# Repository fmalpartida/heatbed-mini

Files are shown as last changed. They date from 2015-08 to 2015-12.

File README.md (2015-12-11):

# heatbed-mini
Mini heatbed for small footprint 3D printers. This bed has been designed for the lewihe play but can be retrofitted to other small 
printers with a print area of 100x100 mm.

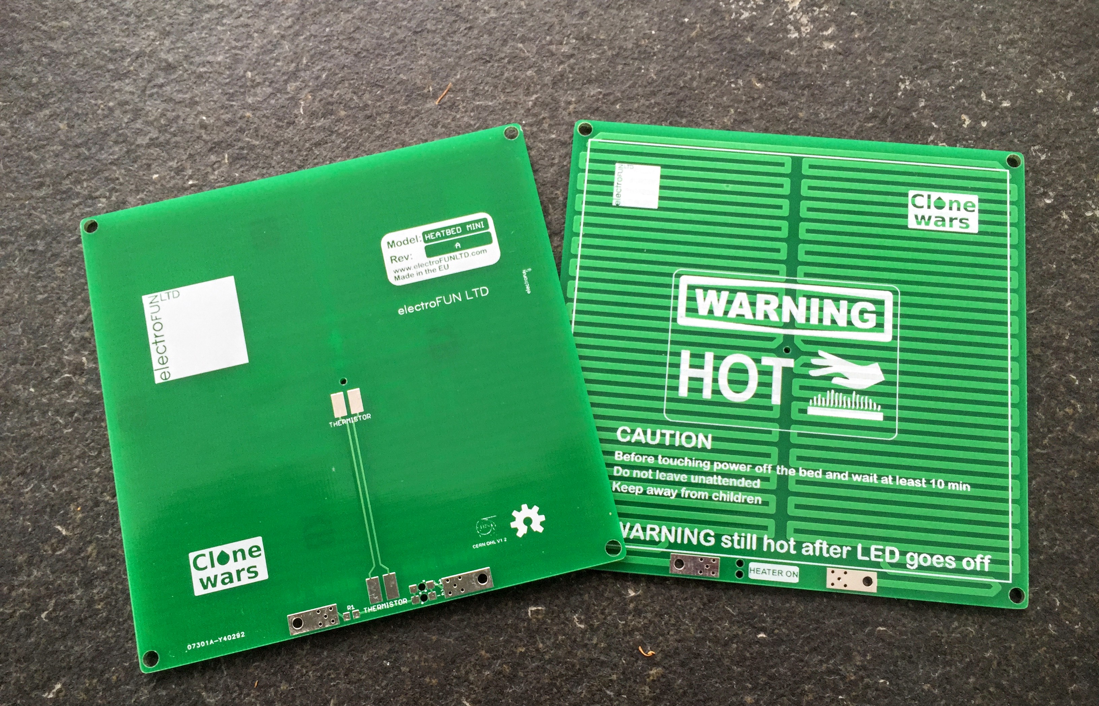
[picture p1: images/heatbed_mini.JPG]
PCB image


## Specifications

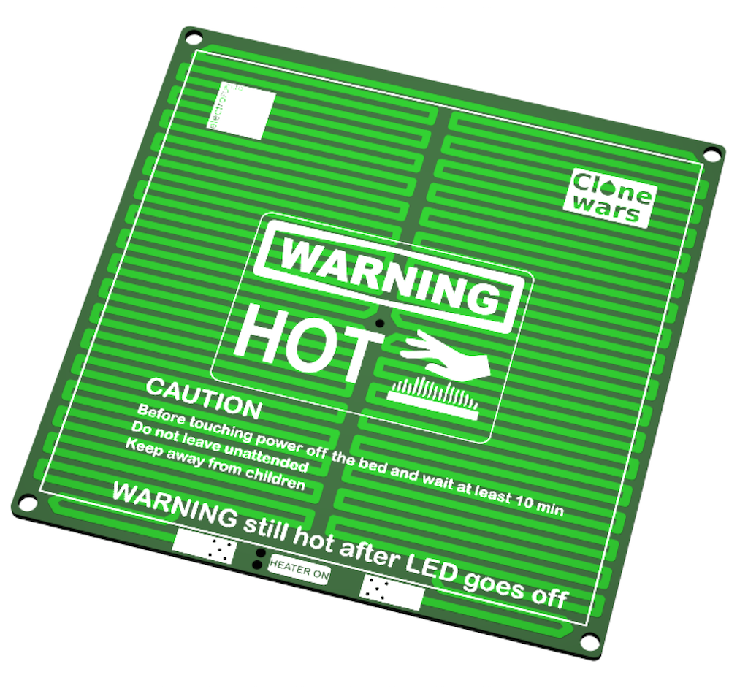
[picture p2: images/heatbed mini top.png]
3D PCB view


+ **Size:** 100x100 mm
+ **Rated voltage:** 12V
+ **Maximum operational temperature:** 150ºC
+ **Power dissipation:**
   + **Rev B:** 69W aprox: 12V @25ºC, 50W aprox: 12V @110ºC 
+ **Resistance:**
   + **Rev B**: 2.1 Ohms aprox, 2.8 Ohms aprox @110ºC
 
Do not exceed rated parameters.

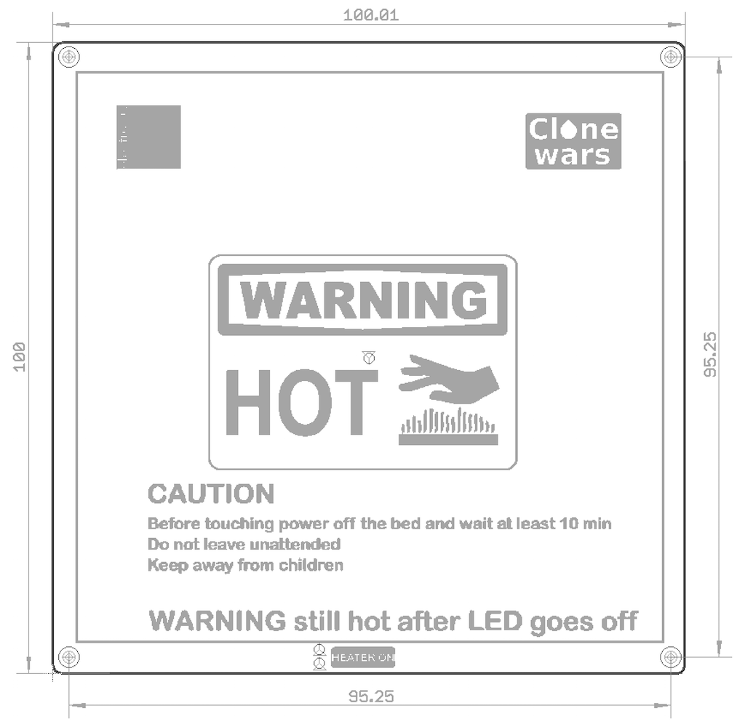
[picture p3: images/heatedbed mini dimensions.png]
PCB dimensions


## Images

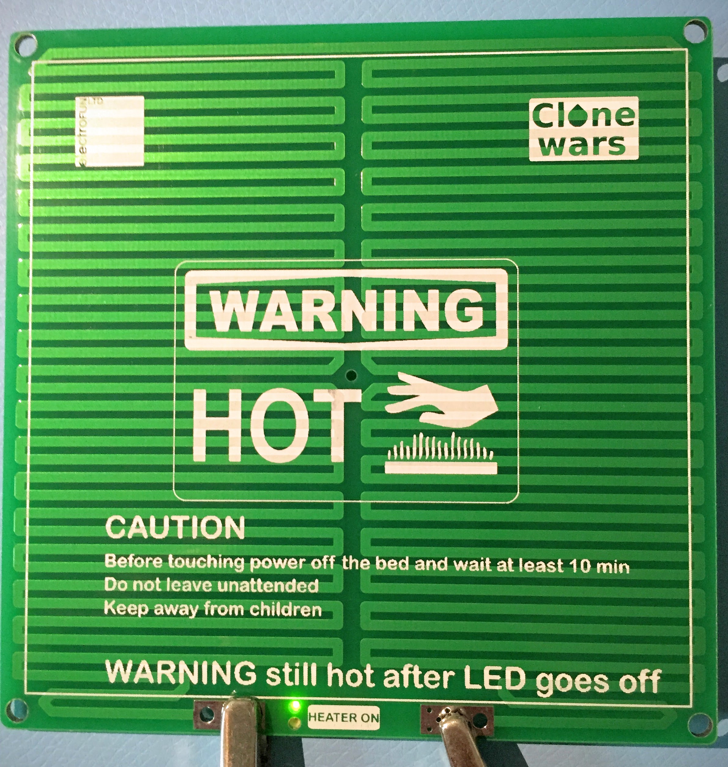
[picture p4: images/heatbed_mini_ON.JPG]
Activated


## License
Released under CERN Open Hardware License v1.2
http://www.ohwr.org/attachments/2388/cern_ohl_v_1_2.txt

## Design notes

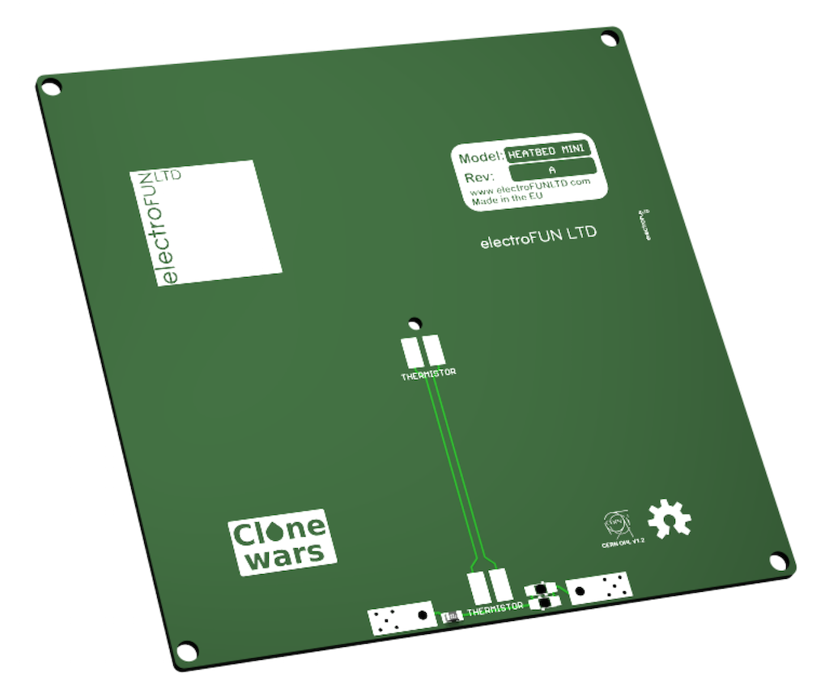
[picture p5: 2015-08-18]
images/heatbed mini bottom.png

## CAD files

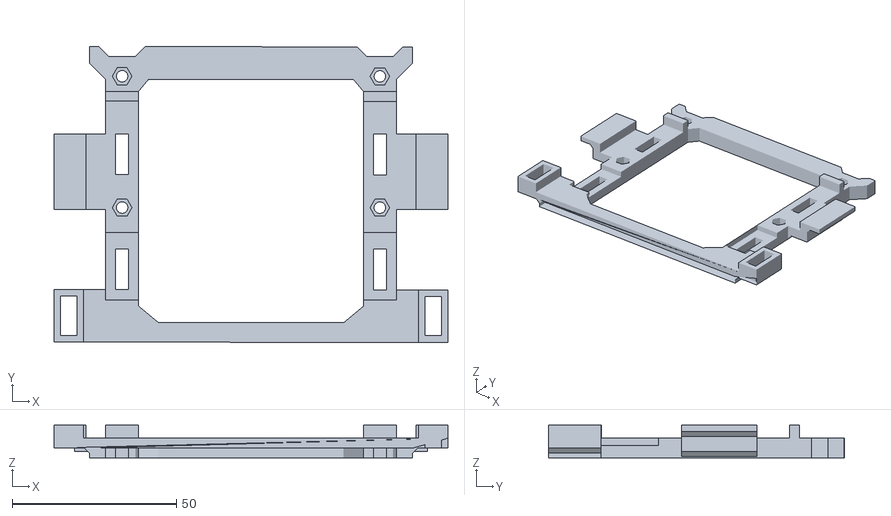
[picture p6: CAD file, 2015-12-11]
3D files/Soporte Base de impresión imanes lewihe Play.stl
120.0 x 90.0 x 10.0

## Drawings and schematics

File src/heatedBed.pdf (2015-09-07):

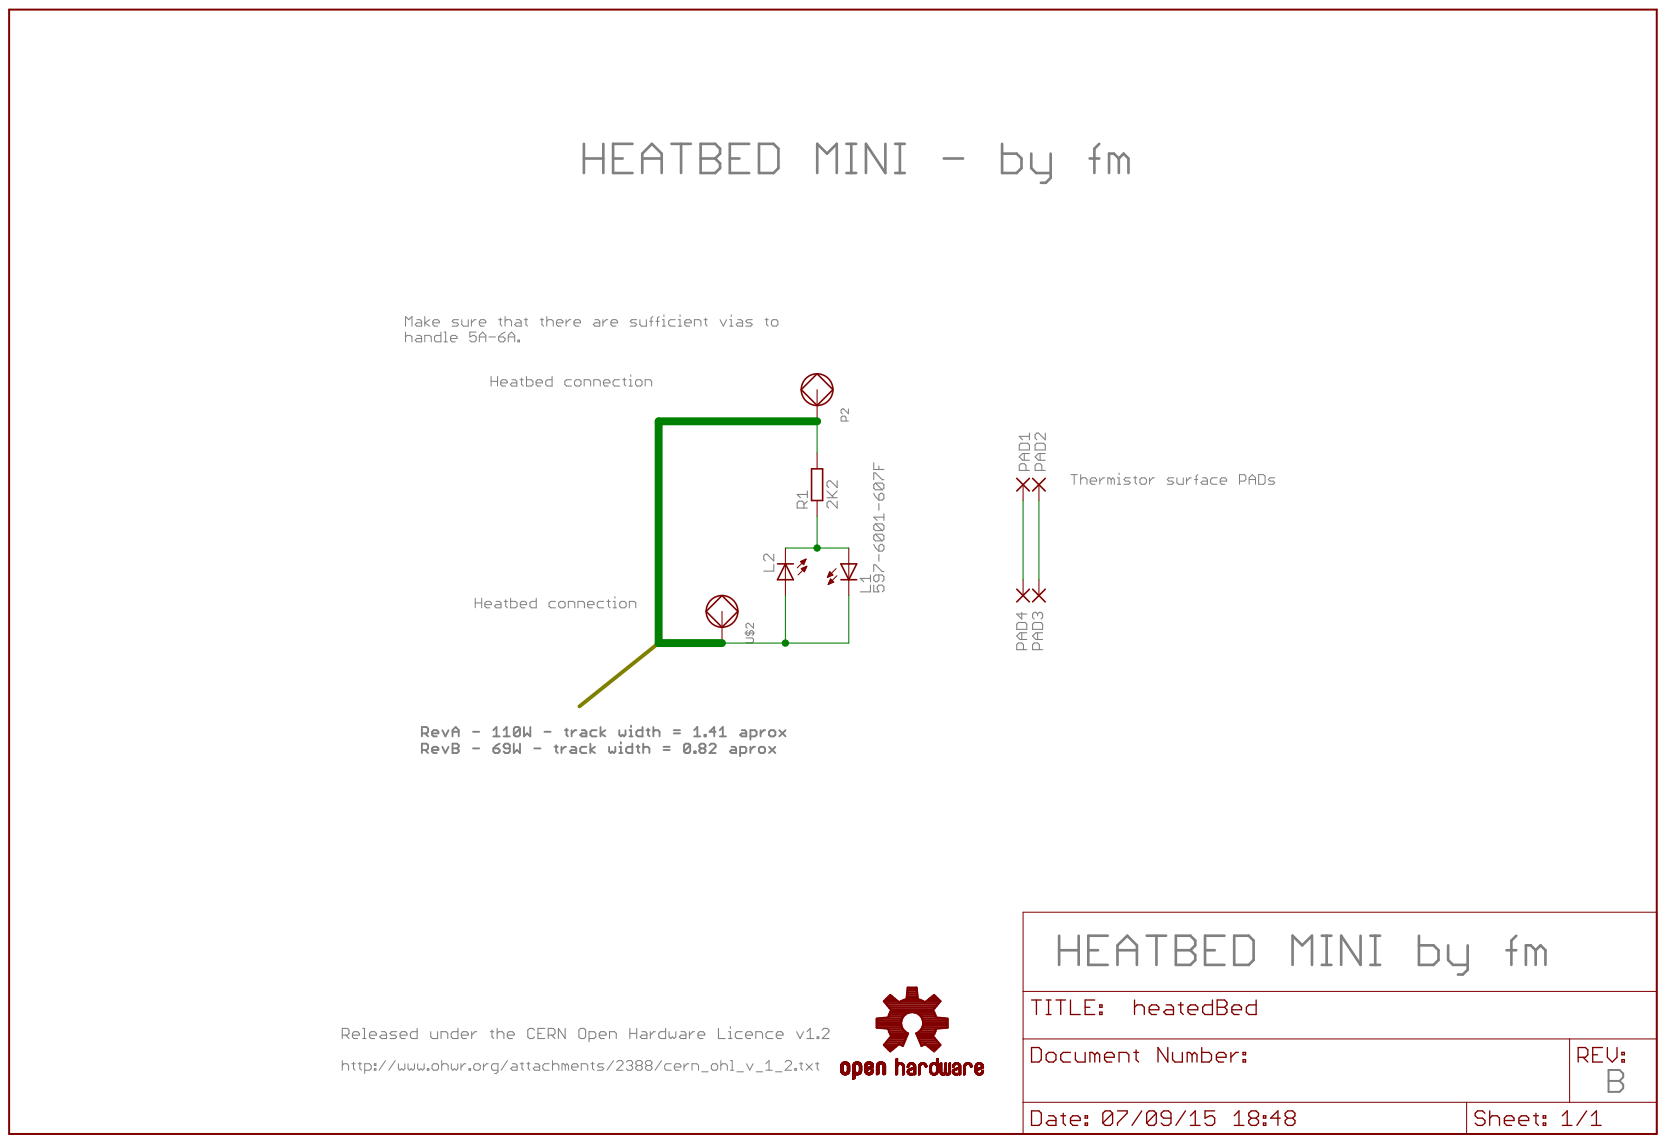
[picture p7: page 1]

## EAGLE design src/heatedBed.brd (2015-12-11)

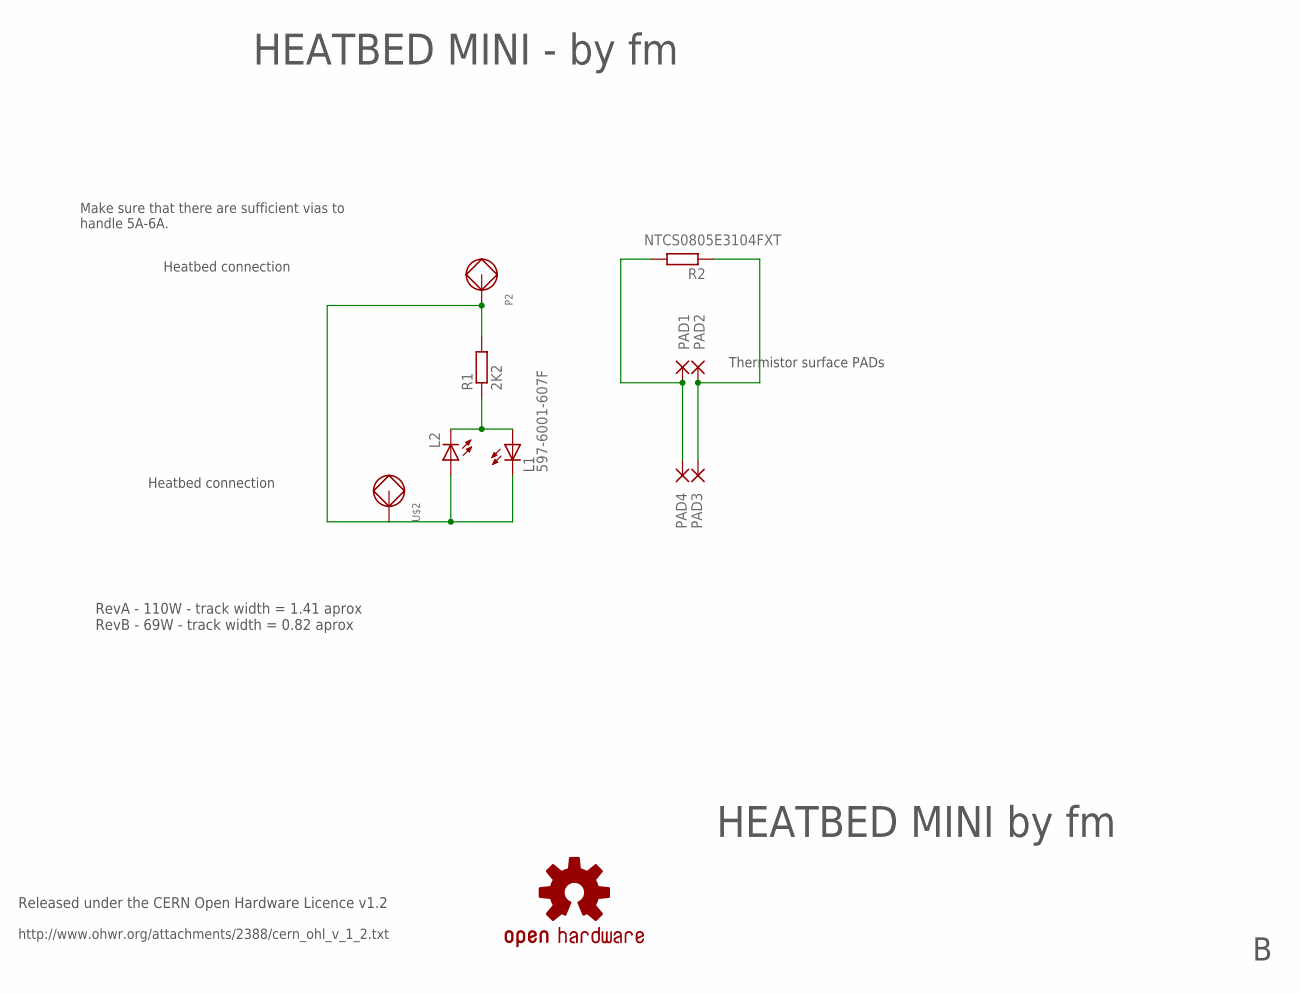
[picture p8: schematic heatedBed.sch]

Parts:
L1: 597-6001-607F; CHIPLED_1206_REVERSE
L2: LEDCHIPLED_1206_REV; CHIPLED_1206_REVERSE
P2: LONG_PAD
PAD1, PAD2, PAD3, PAD4: SMD5; SMD2,54-5,08
R1: 2K2; R0805
R2: NTCS0805E3104FXT; R0805
U$2: LONG_PAD
U$5: SPARKFUN_OSHW-LOGOL; SPARKFUN_OSHW-LOGO-L

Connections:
unnamed: PAD1.1, PAD4.1, R2.2
unnamed: L1.A, L2.C, R1.1
unnamed: PAD2.1, PAD3.1, R2.1
P1: L1.C, L2.A, P2.P$1, P2.P$2, P2.P$3, R1.2, U$2.P$1, U$2.P$2, U$2.P$3

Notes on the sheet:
Released under the CERN Open Hardware Licence v1.2
HEATBED MINI by fm
Heatbed connection
Make sure that there are sufficient vias to handle 5A-6A.
Thermistor surface PADs
http://www.ohwr.org/attachments/2388/cern_ohl_v_1_2.txt
HEATBED MINI - by fm
RevA - 110W - track width = 1.41 aprox RevB - 69W - track width = 0.82 aprox

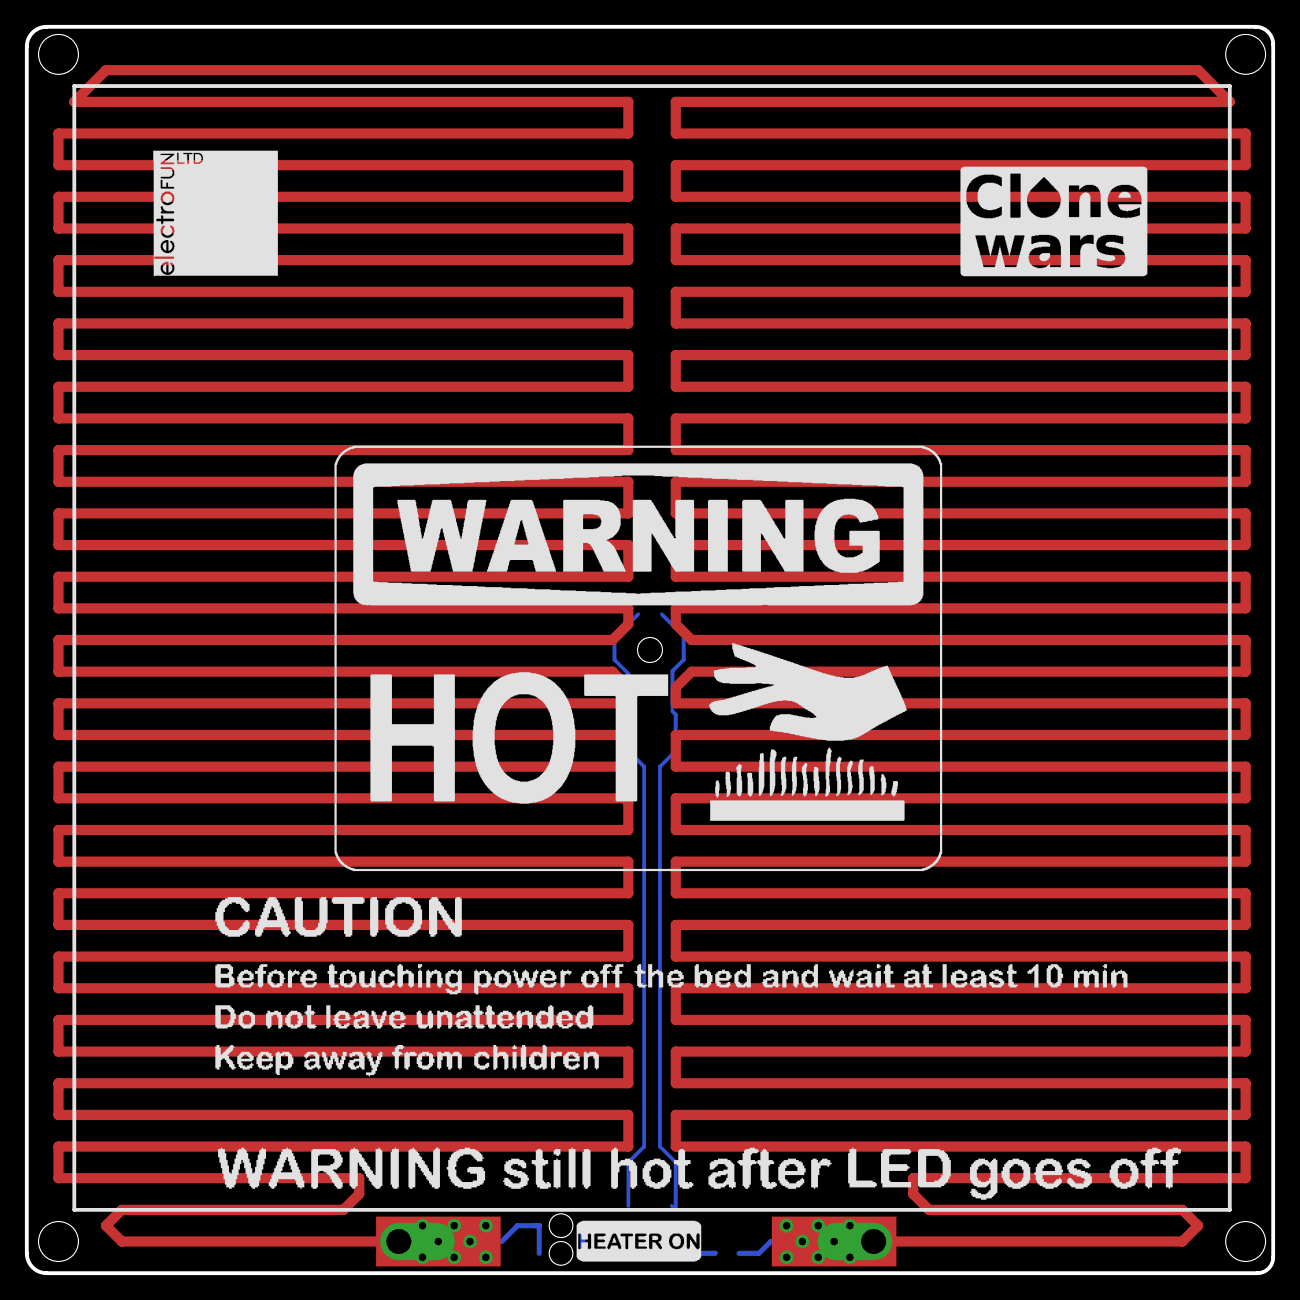
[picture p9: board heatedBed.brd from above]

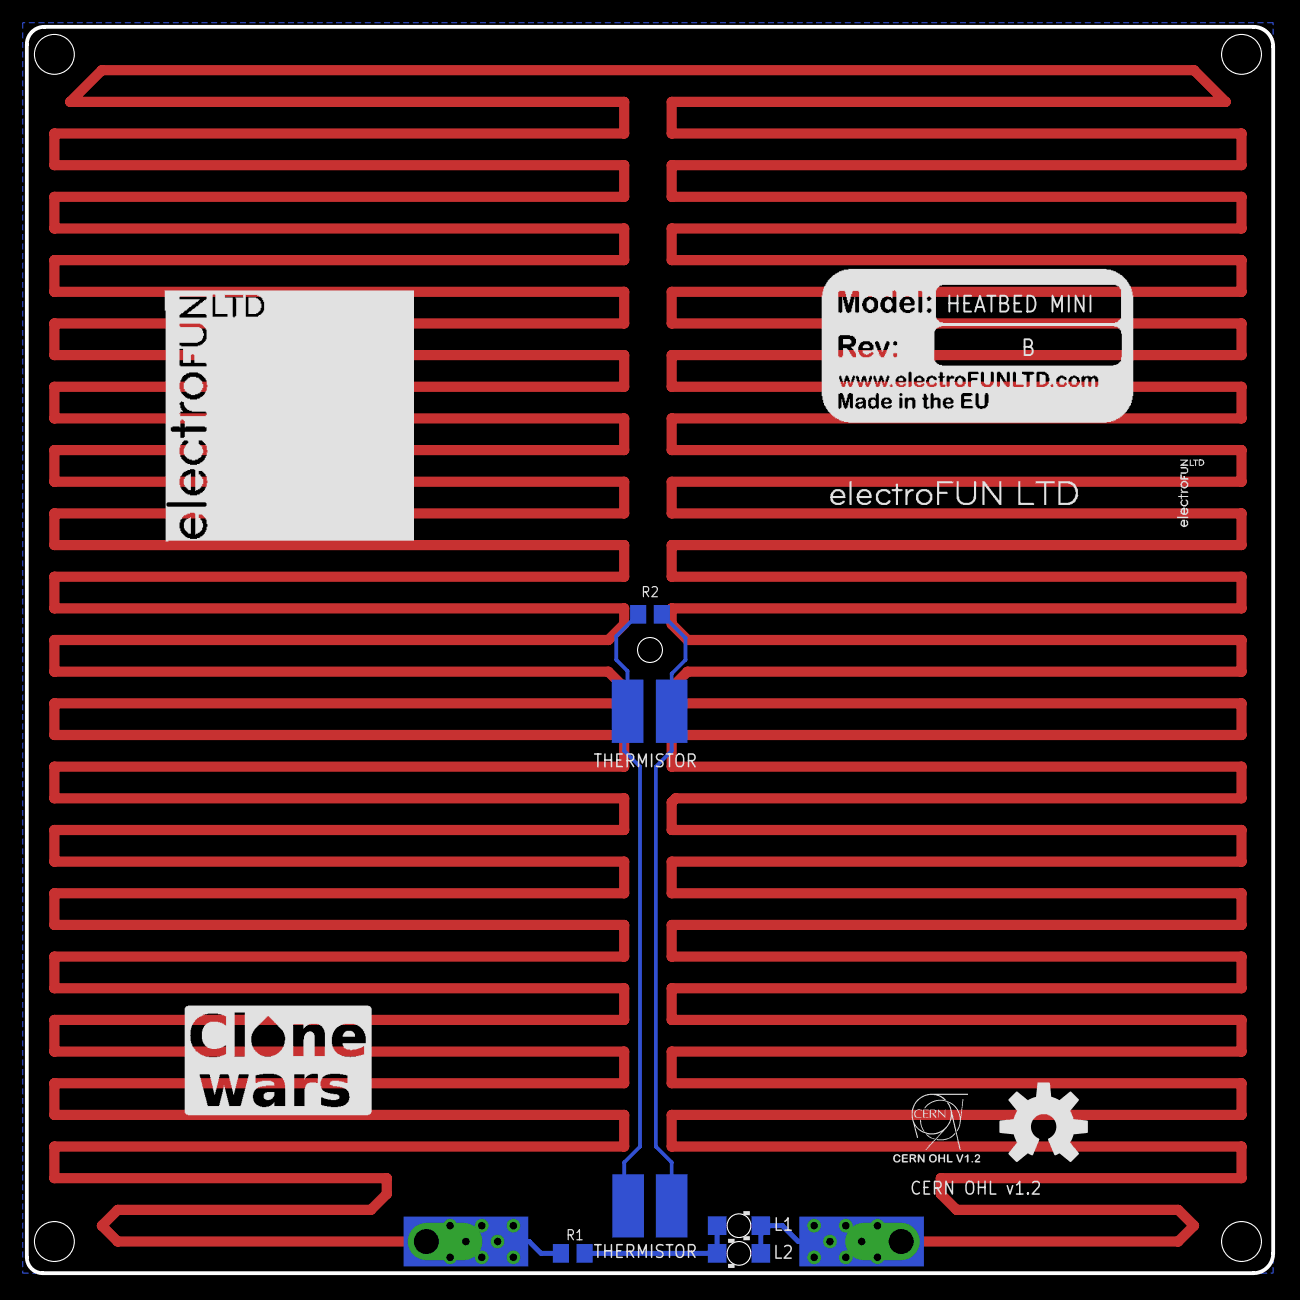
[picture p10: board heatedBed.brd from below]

Board: 2 copper layers, 100.0 x 100.0 mm, 21 parts (14 on the bottom side), 4 nets.

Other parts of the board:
U$1: CAUTION
U$3, U$7: CLONE_WARS
U$4: CERN_OHL
U$6: ELECTROFUN_STRIP
U$8: BOARD_REF
U$9: HEATERON
U$10: WARNING_HOT
U$11: ELECTROFUN_20X20
U$12: ELECTROFUN_10X10

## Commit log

2015-08-18 First version of the mini heatbed for the lewihe play.
    [heatedBed.brd, heatedBed.sch]
2015-08-18 Organized folder structure and added images to the repository.
    [heatedBed.brd, heatedBed.sch]
2015-08-18 Updated PCB for bottom mount LEDs
    [heatedBed.brd, heatedBed.sch]
2015-08-18 Updated silk screen for production prototype run.
    [heatedBed.brd]
2015-08-18 Update schematic pdf file.
2015-08-18 Updated schematic with boar revision and arrangement.
    [heatedBed.sch]
2015-08-19 Added board dimensions and modified drill sizes.
    [heatedBed.brd, heatedBed.sch]
2015-09-07 Preparing to release revision A. Included gerber files
    [heatedBed.GBL, heatedBed.GBO, heatedBed.GBS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]
2015-09-07 Prepare Rev B release.
    [heatedBed.brd, heatedBed.sch]
2015-09-08 Prepared for Rev B.
    [heatedBed.brd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]
2015-09-08 Updated revision B files.
    [heatedBed.brd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]
2015-12-11 Updated files for RevB.
    [heatedBed.brd, heatedBed.sch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]
2015-12-11 Added 3D parts to fit heated.
    [Soporte Base de impresión imanes lewihe Play.stl]
